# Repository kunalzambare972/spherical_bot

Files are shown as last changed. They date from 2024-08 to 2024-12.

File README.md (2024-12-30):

# Spherical-Bot

This repository encapsulates the information related to board dimensions, electronics, sensors and its testing scripts, to controller node for the development of Spherical Bot 2.0

For the software parts and test scrpits of the robot go to this repo : (https://github.com/kunalzambare972/sp-bot) 

## Table of Contents

* [Hardware](https://github.com/kunalzambare972/spherical_bot?tab=readme-ov-file#hardware)
  * [Hardware BOM](#hardware-bom)
  * [PCB Layout and BOM](#pcb-bom-and-layout)
* [Software](https://github.com/kunalzambare972/spherical_bot?tab=readme-ov-file#software)
  * [SD Card Setup](#sd-card-setup)
  * [Software Pre-Requisites](#software-pre-requisites)
  * [IMU Test](#imu-test)
  * [Picamera Test](#picamera-test)
  * [Robot Motion](#robot-motion)
* [Control](https://github.com/kunalzambare972/spherical_bot?tab=readme-ov-file#control)
  * [Pitch Control](#pitch-control)
  * [Roll Control](#roll-control)

# Hardware

## Hardware BOM

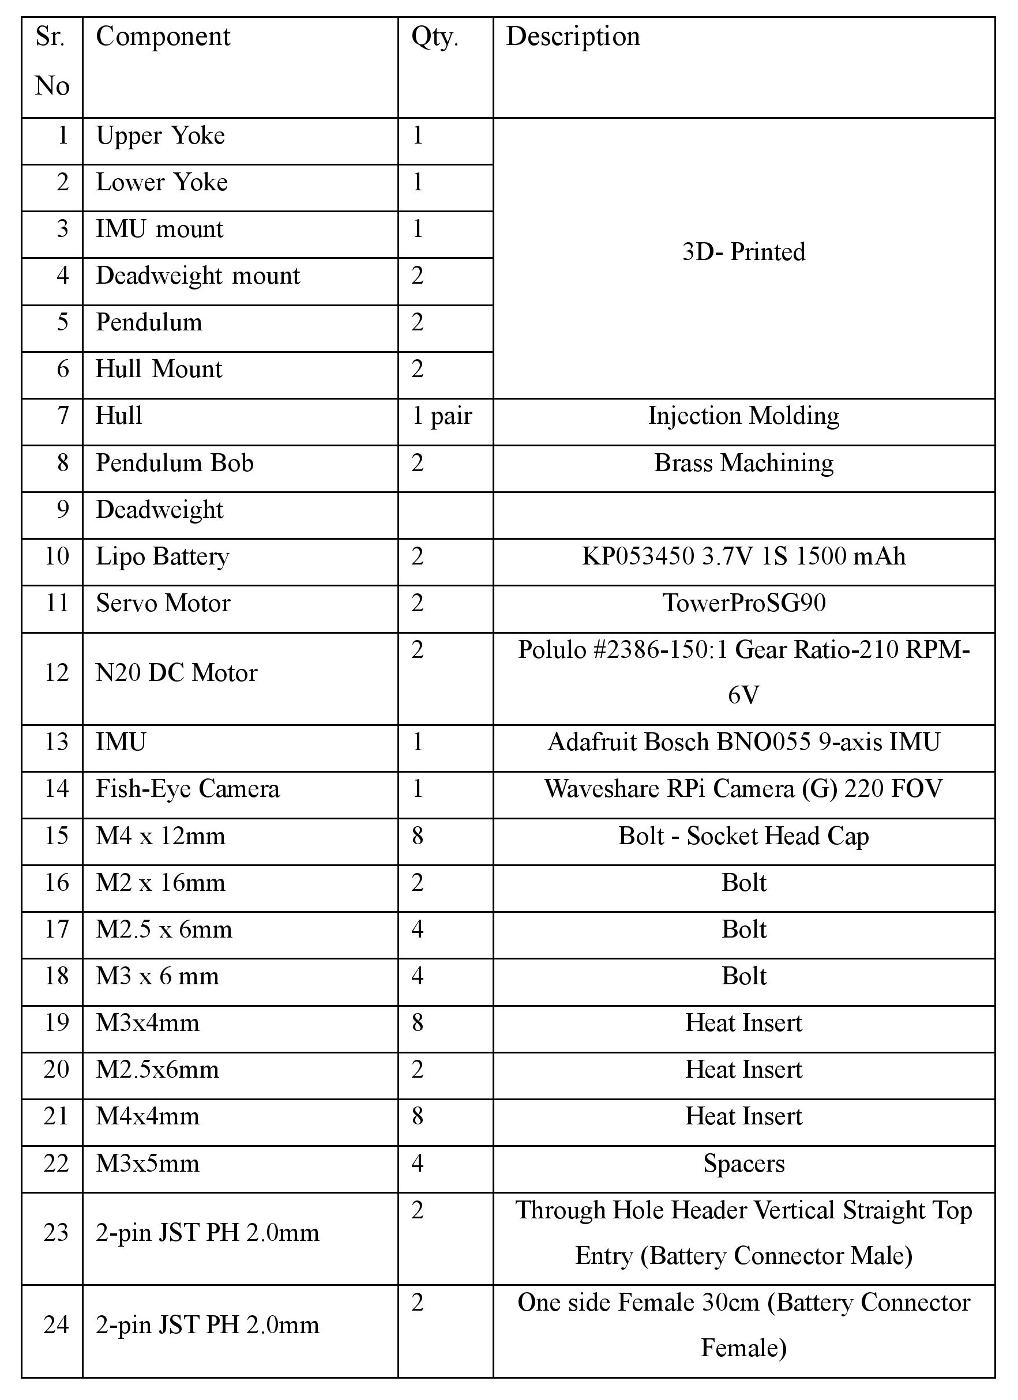
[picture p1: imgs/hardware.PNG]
<p align="center"> 
<br/>

## PCB BOM and Layout

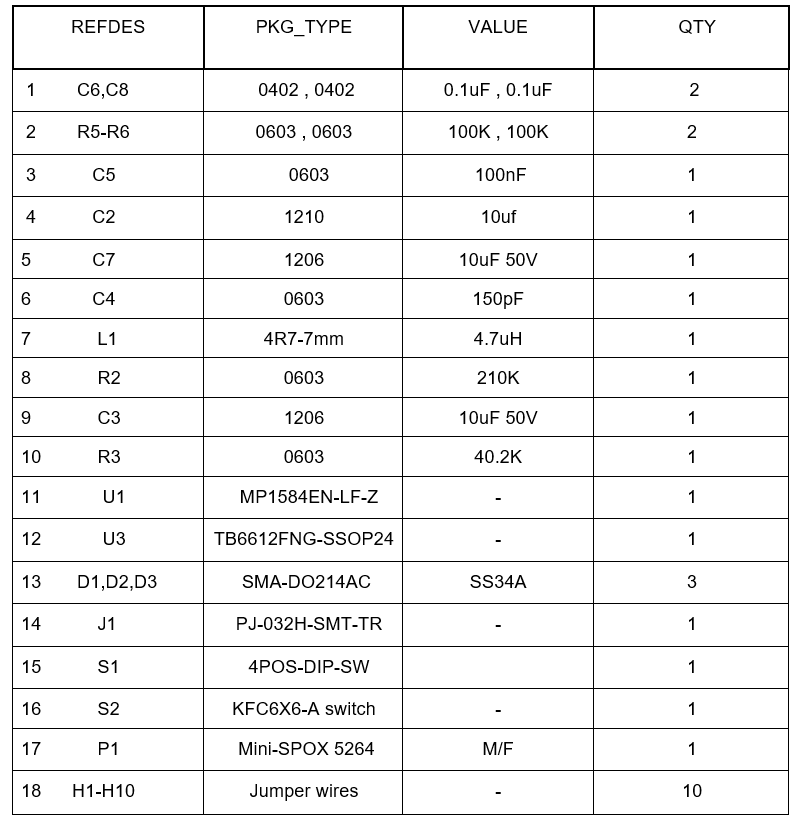
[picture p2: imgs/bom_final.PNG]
Final BOM
<p align="center"> 
<br/>

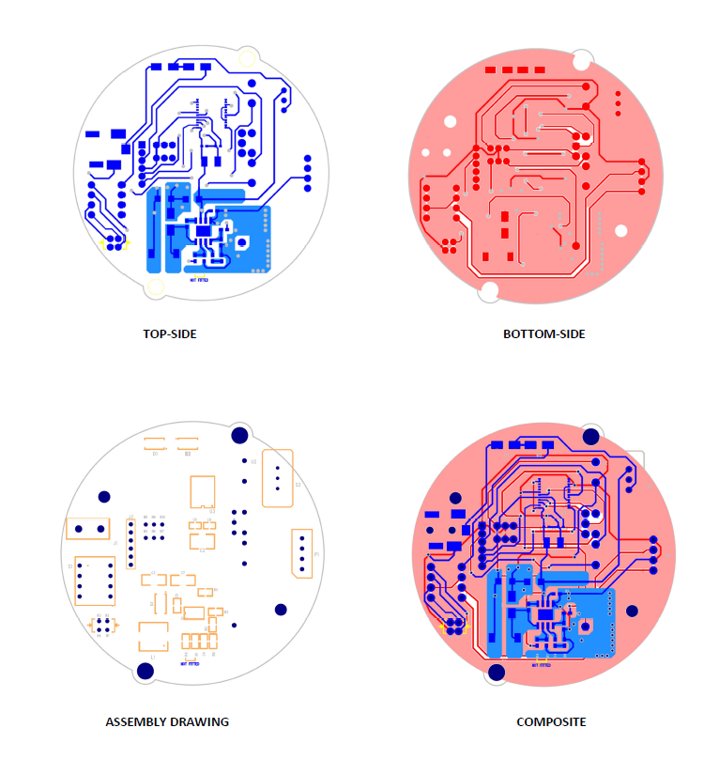
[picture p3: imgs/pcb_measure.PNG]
PCB Dim
<p align="center">
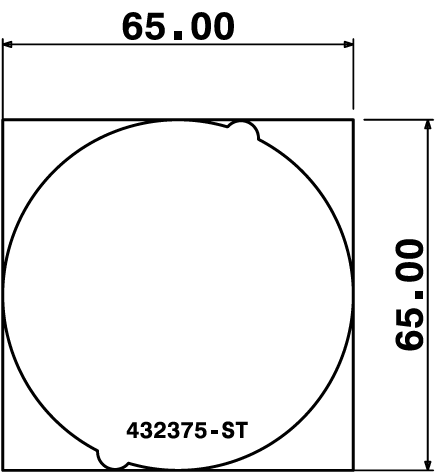
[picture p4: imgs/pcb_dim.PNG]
Overall Board Dimension


# Software

## SD Card Setup

1. Download the Raspberry Pi Imager<br/>
   The easiest way to set up an SD card is by using the Raspberry Pi Imager tool.<br/>
   i. Download Raspberry Pi Imager from the official website of raspberry pi.<br/>

2. Install Raspberry Pi Imager<br/>
   i. Windows/Mac: Run the downloaded installer and follow the on-screen instructions.<br/>
   ii. Linux: For Ubuntu, you can install it directly via the terminal:
   ```
   sudo apt install rpi-imager
   ```
3. Insert the microSD card into your computer using an SD card reader.
4. Launch Raspberry Pi Imager on your computer.
5. Choose the Device in Raspberry Pi Imager which is Raspberry Pi Zero W.
6. Choose the OS in Raspberry Pi Imager which is Raspberry Pi OS (32-bit)- Debian Bookworm.
7. Select the SD Card which is connected to the computer.
8. Advanced Settings<br/>
   i. Access the advanced settings by pressing "Ctrl+Shift+X" before clicking Next/Write.<br/>
   ii. Set the hostname to "spbot"<br/>
   iii. Set the username as "sp"<br/>
   iv. Set your password.<br/>
   v. Configure Wi-Fi: Enter your Wi-Fi SSID and password if you want the Raspberry Pi to connect to Wi-Fi automatically.<br/>
   vi. Enable the SSH in the Services Section of Advanced Settings.<br/>
   vii. Click on "SAVE"<br/>
9. Click on Next/ Write and the Raspberry Pi Imager would start to write the SD card with Raspberry Pi OS(Linux).
10. Once done eject the SD card from the computer and insert it into Raspberry Pi for first boot.
    
## Software Pre-Requisites
1. Firstly we need to clone the software package github repositroy in raspberry pi file system. Since the repository is private you need to generate a personal access token for cloning the directory<br/>
  To generate a personal access token :-<br/>
   i. Go to your Github Settings >> Developer Settings >> Personal Access Tokens.<br/>
   ii. Then click on classic token.<br/>
   iii. Select the expiration date and select "repo" in scopes for full control of private repository.<br/>
   iv. Generate and copy the token. Keep it safe; you won't be able to see it again.<br/>

2. Now open the terminal and run for cloning "sp-bot" repository
```
git clone https://github.com/kunalzambare972/sp-bot.git

```
3. Authenticate<br/>
   i.When prompted for a username, enter your GitHub username.<br/>
   ii.When prompted for a username, enter your GitHub username.<br/>
   
4. Enter the Repository Directory

```
cd sp-bot
```
   
5. Install all the required dependencies  
```
pip install -r requirements.txt
```
The above the steps would help to setup the raspberrypi sdcard for the operation of the robot

## IMU Test

The IMU being used is the Bosch 9-axis BNO-055 sensor -

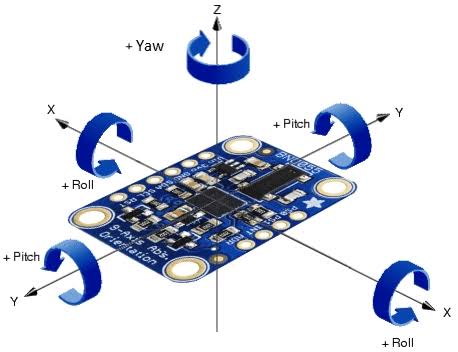
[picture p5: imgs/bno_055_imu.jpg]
BNO_IMU
<p align="center"> 
<br/>

### Plotting the IMU result

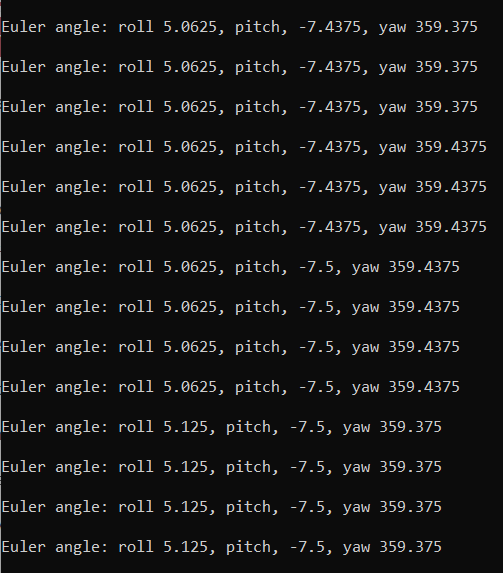
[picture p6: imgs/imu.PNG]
IMU_command_line
<p align="center">
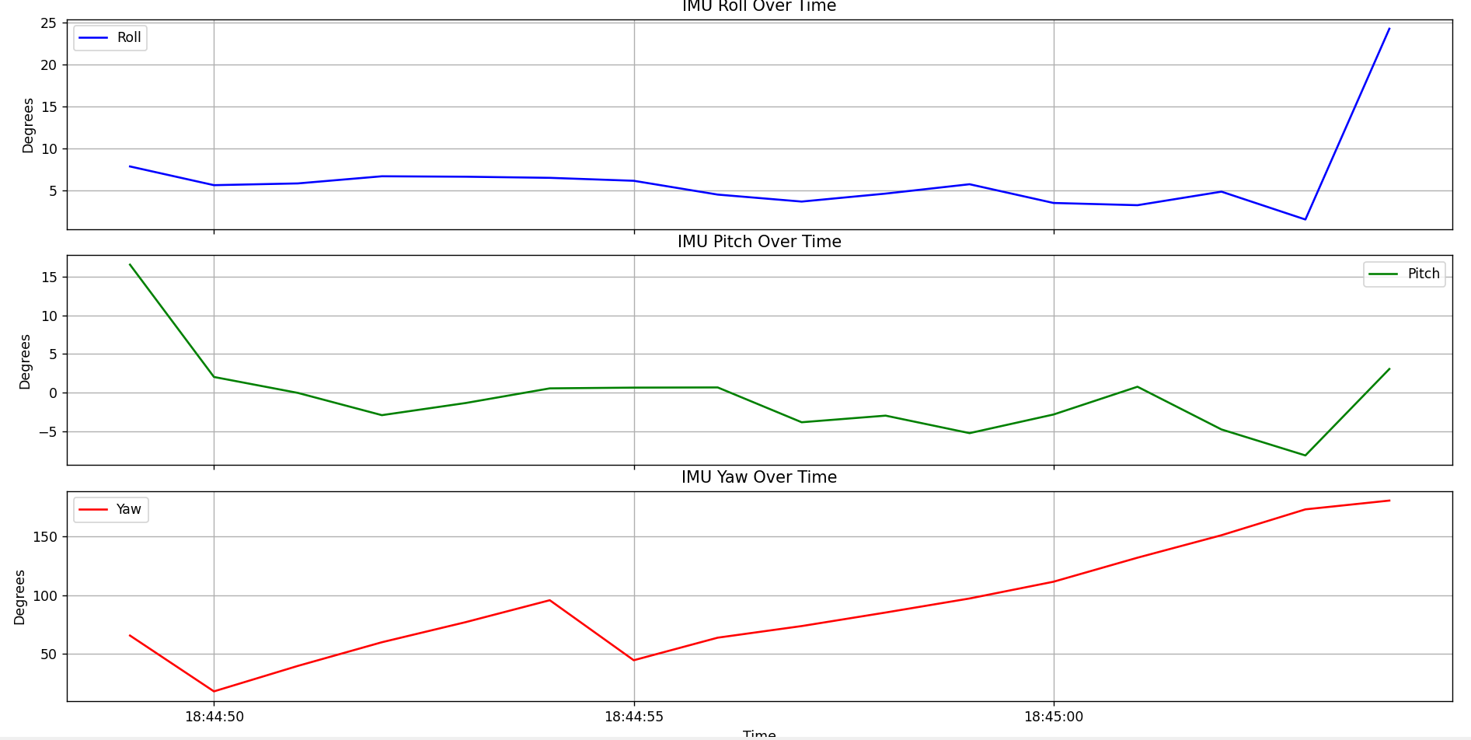
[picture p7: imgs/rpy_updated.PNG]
IMU_graph


### To test the IMU output - 

1. Navigate to sensor_tests/IMU_test directory
2. Run the test_imu.py

## PiCamera Test

The Camera being used is the Waveshare OV5647 220FOV Camera -

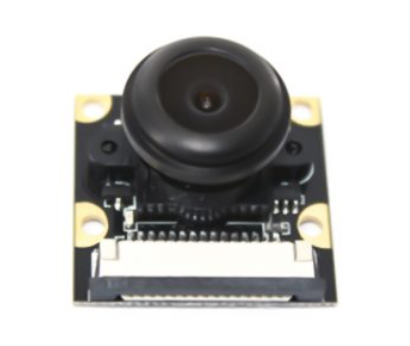
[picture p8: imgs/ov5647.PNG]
Camera
<p align="center"> 
<br/>

### Viewing the output from camera

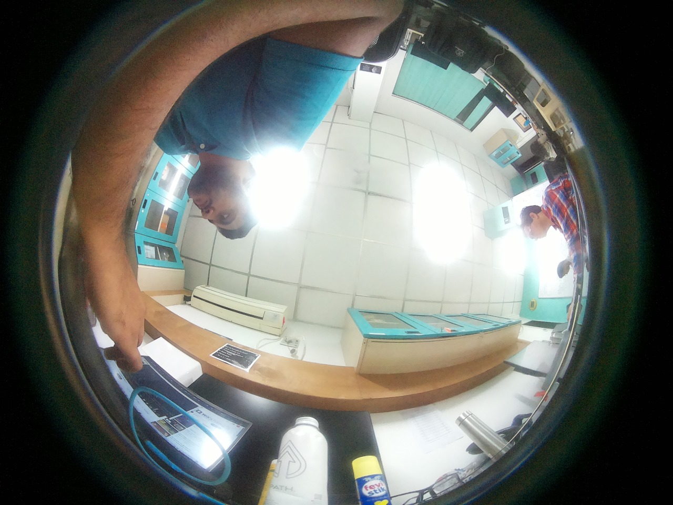
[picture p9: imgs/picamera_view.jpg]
Cam_output
<p align="center">
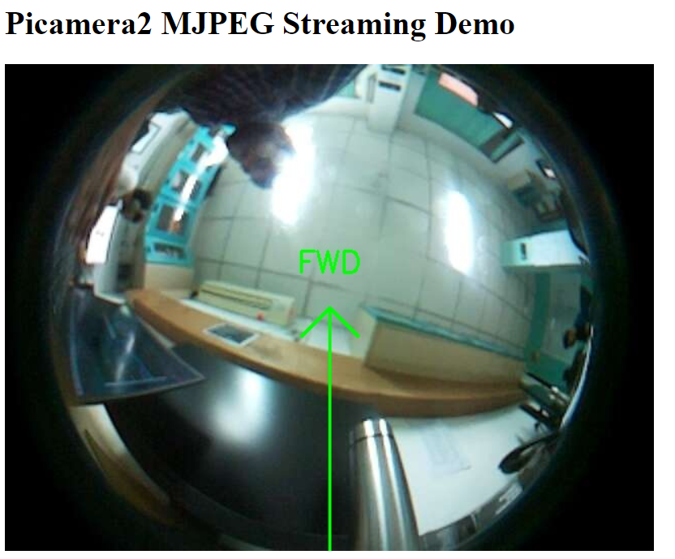
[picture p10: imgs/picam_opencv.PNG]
Cam_fw_output


### To test the camera output - 

1. Note down the system's IP
2. Navigate to sensor_tests/Picamera_test directory
3. Run the test_picam2.py
4. Head to the following page - http://{IP_ADDRESS or spbot.local}:5000/

## Robot Motion

The following clip shows the robot's forward movement - 

https://github.com/user-attachments/assets/1400048a-bb1d-4988-941b-7a97be991c32

The following clip shows the robot's forward and backward movement -

https://github.com/user-attachments/assets/daac4932-1899-4ce8-a5ff-24615ddae6e5

# Control

## Pitch Control

### Methodology
The pitch control of the Spherical Bot is managed using a Proportional Controller (P-controller). The control strategy is implemented to maintain the desired pitch angle by adjusting the servo motors and the N20 motor based on the feedback from the IMU sensor.

### Mathematical formula

The Proportional Control equation used is:

$$
P_{\text{error}} = \text{Set Point} - \text{Actual Pitch}
$$

$$
\text{Motor PWM} = \max(0, \min(200, K_p \times P_{\text{error}} + \text{User PWM}))
$$

where:
-  $$  P_{\text{error}} $$ is the pitch error.
- $$ \( \text{Set Point} \) is the desired pitch angle (set to 0.0 degrees in this case).
- $$ \( \text{Actual Pitch} \) is the current pitch angle measured by the IMU sensor.
- $$ \( K_p \) is the proportional gain, set to 0.00876.
- $$ \( \text{User PWM} \) is a constant value (set to 185) that provides the base motor speed.
- $$ \( \text{Motor PWM} \) is the calculated PWM value to drive the motor, ensuring it stays within the range of 0 to 200

### Optimal Value

The optimal proportional gain $$ (\( K_p \)) for achieving stable pitch control is determined to be:

$$ \[ K_p = 0.00876 \]

## Roll Control

### Methodology

The roll control of the Spherical Bot is managed using a Proportional Controller (P-controller). The control strategy is implemented to maintain the desired roll angle by adjusting the servo motors and the N20 motor based on feedback from the IMU sensor.

### Mathematical Formula

The Proportional Control equation used is:

$$
P_{\text{error}} = \text{Set Point} - \text{Actual Roll}
$$

$$
\text{Motor PWM} = \max(0, \min(200, K_p \times R_{\text{error}} + \text{User PWM}))
$$

where:
- \( R_{\text{error}} \) is the roll error.
- \( \text{Set Point} \) is the desired roll angle (set to 0.0 degrees in this case).
- \( \text{Actual Roll} \) is the current roll angle measured by the IMU sensor.
- \( K_p \) is the proportional gain, set to 0.00876.
- \( \text{User PWM} \) is a constant value (set to 185) that provides the base motor speed.
- \( \text{Motor PWM} \) is the calculated PWM value to drive the motor, ensuring it stays within the range of 0 to 200.

### Optimal Value

The optimal proportional gain (\( K_p \)) for achieving stable roll control is determined to be:

\[ K_p = 0.00876 \]

## License

This project is licensed under the MIT License - see the [LICENSE](LICENSE) file for details.

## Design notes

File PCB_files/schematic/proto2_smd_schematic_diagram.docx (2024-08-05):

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
10uF 5~~0V~~

100K

C5

U1 ⁸

BST

⁷VIN

100nF 1

L1

4.7 uH

15uH

22uF 6~~.3V~~

OUT

GND

C1

42 31

R4

2

SW

4

D3

10

C3

8642

GND GND

GND

6

EN

FREQ

FB

CMP

GND

3

C4

GND GND R2

210K

B

H3 H4 H2 H1 +ve2

7531

S1

GND

R1

24.9K 100K R5

5

GND

150pF

40.2K

R3

B

+ve1

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
³ IO1

GND GND

100K

R6

GND

GND

3

V

3

27

~~C~~1

28

~~C~~2

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
IO10 IO11 IO12 IO13 IO14 IO15 IO16 IO17 IO18 IO19 IO20 IO21 IO22 IO23 IO24 IO25 IO26

5

7

8

10 11 12 13 15 16 18 19 21 22 23 24 26 29 31 32 33 35 36 37 38 40

Pin 13 -> Pin 19 STBY Motor driver OUT

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
G1G2G3G4G5G6G7G8

4

0

5

0

4

9

A

691GND

2

2

3

3

U3

3

C8

0.1uF GND

A

C1 C2

¹ A01

VM1

24

VIN

OUT GND

4 1

3 2 J2

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
A01_1

PGND1

PGND1_1 A02

A02_1

B02

B02_1

PGND2

PWMA AIN2 AIN1 VCC

STBY GND

BIN1 BIN2

23 22 21 20 19 18 17 16

C2

10uF

C6

0.1uF

TITLE

Schematic1

Corrected Schematic

10

11

GND

12

GND

PGND2_1 B01

B01_1

PWMB VM3 VM2

15 14 13

GND

1

DWG NO001 modified by Akash Shenil

MODIFIED BY

AKASH SHENIL

SIZE REV A4

DRAWN BY

GIRISH GIRI

SCALE of

SHEET

INCH 1 2 24/02/2020:21:56 27/09/2023 27/09/2023

27-09-2023

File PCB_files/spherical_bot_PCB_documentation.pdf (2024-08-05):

# SPHERICAL BOT

## DUAL-LAYER, UTILITY CIRCUIT BOARD

### DESCRIPTION

The Utility Circuit Board (UCB) is adual-layer, surface mount technology-based board designed to combine 3+ functional blocks on a single PCB. The objective is to achieve modularity, minimize repair and diagnostic issues with a form factor optimum to the SPEHRICAL BOT mechanical constraints.

### FEATURES

The UCB features following utilities:

- MP1584 - 3A, 1.5MHz, 28V Step Down Converter Logic.
- TB6612FNG – 4 mode Motor Driver Logic.
- Raspberry Pi Zero W compatibility.
- Charging Mode with Dual Series Battery input and External Supply Logic.
- Reverse current protection logic.

### APPLICATIONS

- Power Input.
- Battery Charging.
- Control In/Outs.
- High voltage conversion.
- Current Conversion.
- Reverse Input Protection.

### SOFTWARE

The schematic for PCB is designed on DxDesigner Software. The layout is designed and developedon PADS v9.5 and both these platforms are a part of software package tool suite from Mentor Graphics, Siemens. The schematic design is developed by implementing universal standard symbol library and can be used to migrate decal layout libraries in PADS logic for layout designing. The foot print for each component is developed from scratch by referring to respective datasheet constraints for decal guidelines.
The routing for layout is developed with optimum designing rules for trace length and width. The board design ensures all requisite IPC standard and EMI, EMC considerations are met. All placements and routing are done with strictly referring to PCB layout Guidelines wherever needed and mentioned in components datasheets.

### BLOCK DIAGRAM

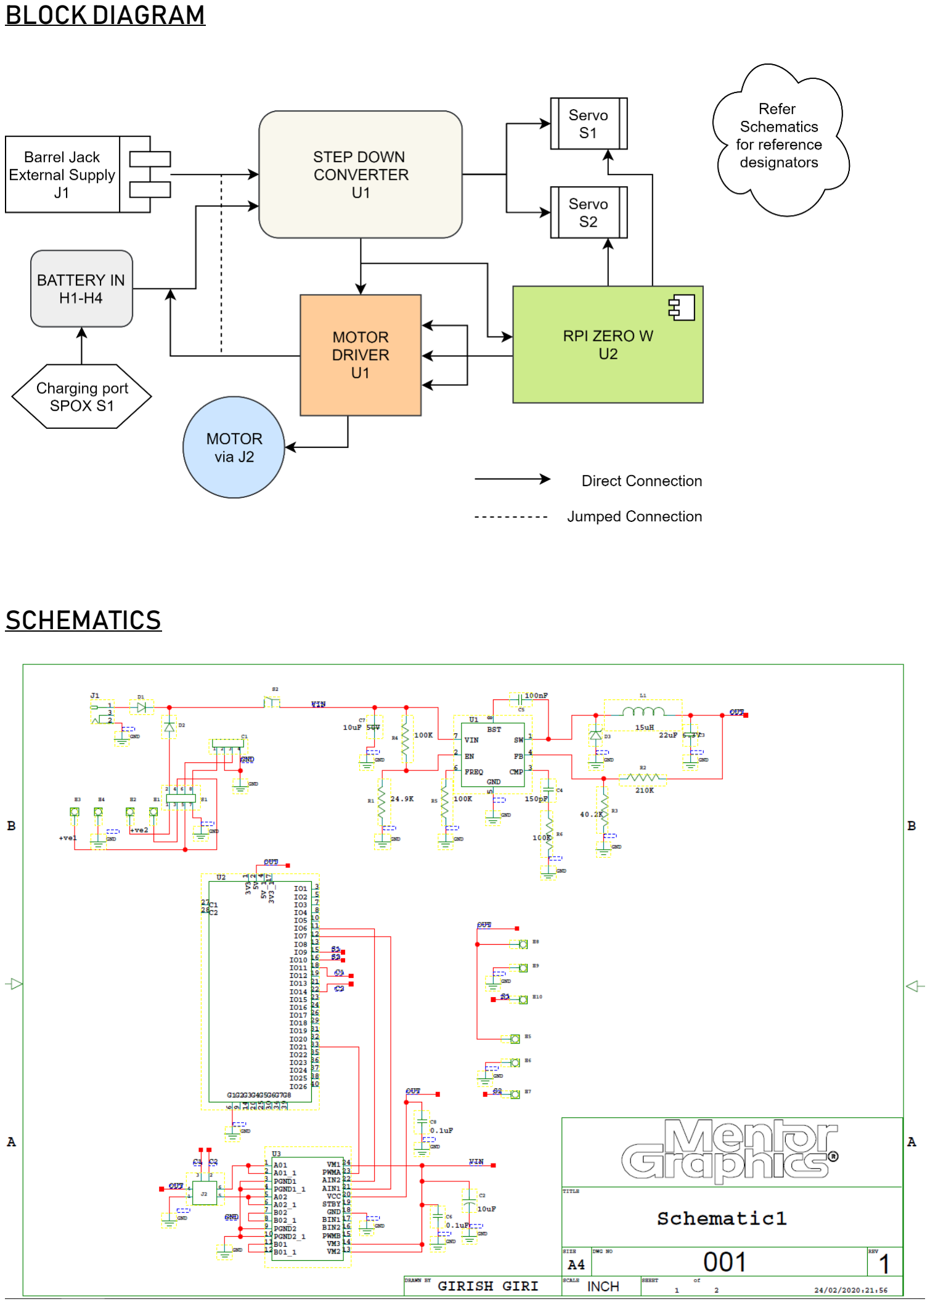
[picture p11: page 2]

### SCHEMATICS

### LAYOUT

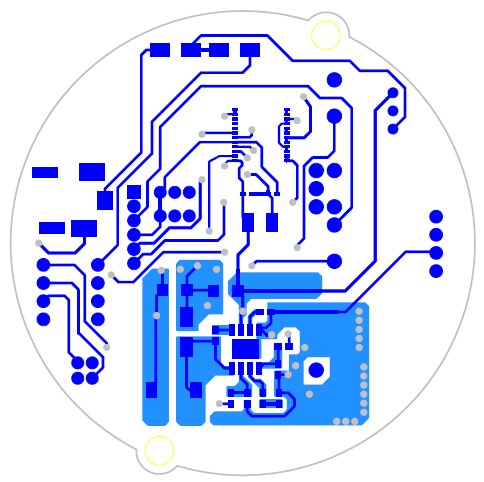
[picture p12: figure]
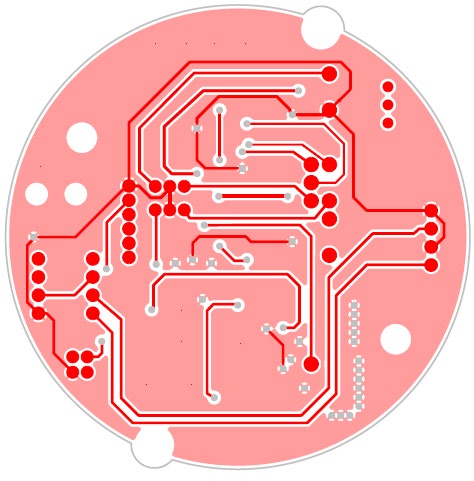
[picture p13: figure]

TOP-SIDE | BOTTOM-SIDE

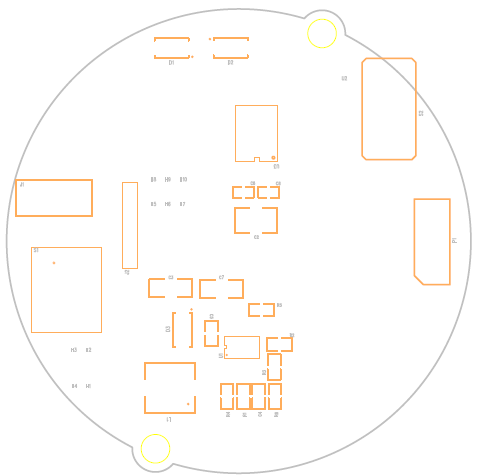
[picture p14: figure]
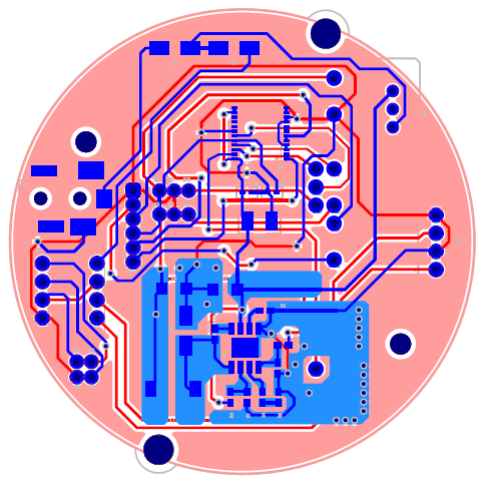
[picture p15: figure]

ASSEMBLY DRAWING | COMPOSITE

### CAD MODELLING

The PADS layout file designed for the PCB is exported in CAM planes to generate GERBER files for PCB Fabrication. The same Layout File can be exported in .iso format supported in CircuitWorks, which is an extension available in SolidWorks 2017. CircuitWorks allows user to view the layout design into actual 3D phase and also features editable components library which can be updated by manually searching for the part files of each component online and adding it in the same. Once all components are added, the build command generates and assembly file with available components mounted on board as shown in figure above. The above process gives a very near perfect idea about the utility board before its fabrication and assembly.

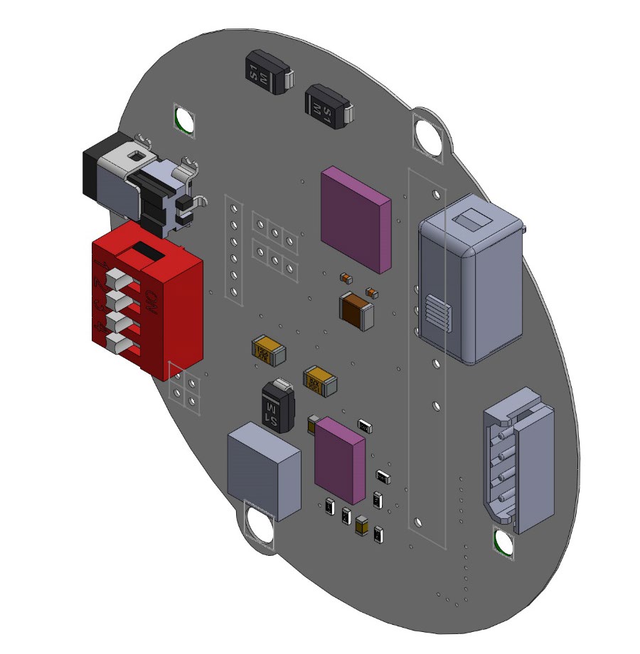
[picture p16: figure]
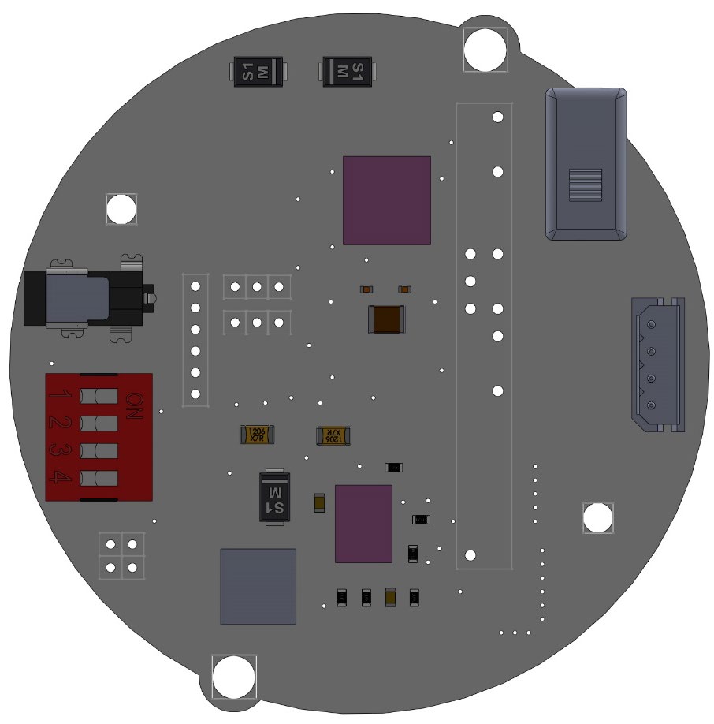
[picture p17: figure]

Almost all the components (SMD and Through Hole) are mounted on top side to maintain isolation with motors at the bottom. The utility board is designed to sustain permissible current and voltage
ratings | provided | by
manufacturers, | with
consideration of safe positive
tolerance | values. | The
components selection is based on ratings and package availability. The placement of each device is done to ensure compatibility with bot mechanics keeping accessible terminals exposed. Thermal areas and isolations are provided wherever required for heat dissipation.

### REFERENCES

Kindly refer to Datasheets, BOM, Schematics and Layout Docs and CAD drawings from the PCB Fabrication and Development Folder Zip folder for design logic, component values/counts, package types, Drill Holes, Board Outline, specifically Components datasheet for PCB Layout Guidelines, Fabricator details and other relevant information.

### NOTE

The information in this document is subject to changes but should only be done with prior notice to Vaibhav Kadam, Research Assistant Spherical Bot. The information changes should be only in the form of an update, any direct changes require notification from the user. Users should warrant and guarantee that no information and data is manhandled, misplaced or affected in a way that leads to additional work of already done job. The data in this Document and all the other relevant information in PCB Fabrication and Development Folder Zip is abides by the said disclaimer.

# SPHERICAL BOT

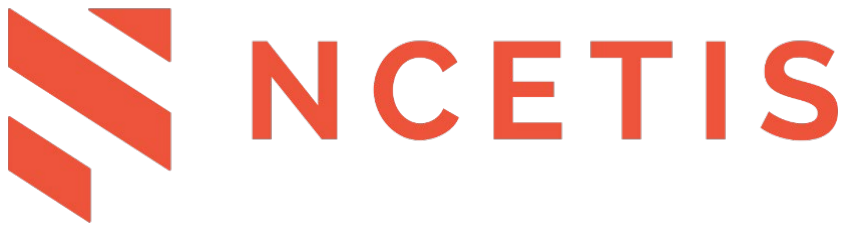
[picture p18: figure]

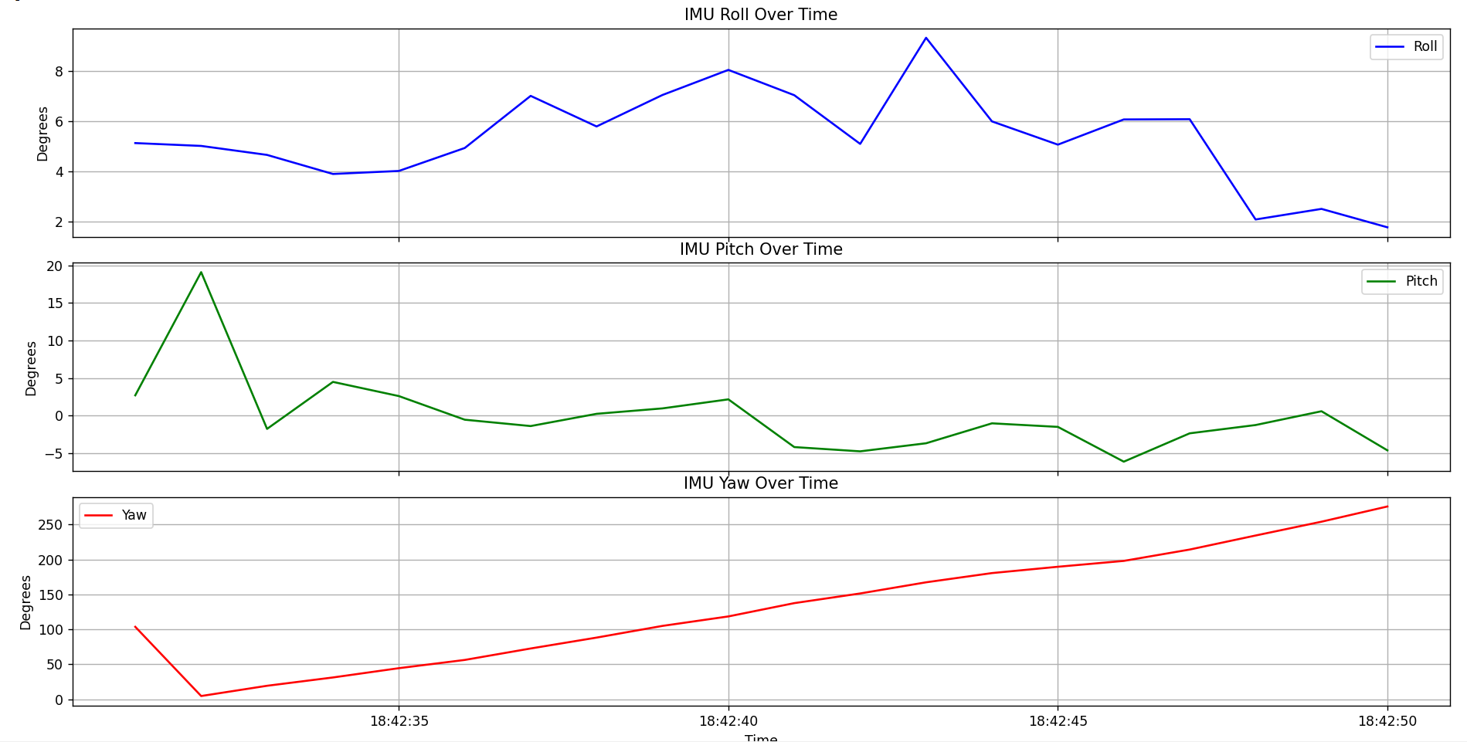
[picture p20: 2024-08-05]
imgs/rpy_updated_2.PNG

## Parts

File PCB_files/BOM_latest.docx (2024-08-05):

Part Lister output for Board1

Generated on Monday, February 24, 2020

Modified on Thursday, October 5, 2023 by Akash Shenil.

REFDES | PKG_TYPE | VALUE | QTY
1 C6,C8 | 0402 , 0402 | 0.1uF , 0.1uF | 2
2 R5-R6 | 0603 , 0603 | 100K , 100K | 2
3 C5 | 0603 | 100nF | 1
4 C2 | 1210 | 10uf | 1
5 C7 | 1206 | 10uF 50V | 1
6 C4 | 0603 | 150pF | 1
7 L1 | 4R7-7mm | 4.7uH | 1
8 R2 | 0603 | 210K | 1
9 C3 | 1206 | 10uF 50V | 1
10 R3 | 0603 | 40.2K | 1
11 U1 | MP1584EN-LF-Z | - | 1
12 U3 | TB6612FNG-SSOP24 | - | 1
13 D1,D2,D3 | SMA-DO214AC | SS34A | 3
14 J1 | PJ-032H-SMT-TR | - | 1
15 S1 | 4POS-DIP-SW | | 1
16 S2 | KFC6X6-A switch | - | 1
17 P1 | Mini-SPOX 5264 | M/F | 1
18 H1-H10 | Jumper wires | - | 10

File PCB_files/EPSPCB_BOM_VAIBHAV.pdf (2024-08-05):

Part Lister output for Board1
Generated on Monday, February 24, 2020
# | REFDES | PKG_TYPE | VALUE | QTY

| 1 C6,C8 | 0402,0402 | 0.1uF,0.1uF | 2
| 2 R4-R6 | 0603,0603,0603 | 100K,100K,100K | 3
| 3 C5 | 0603 | 100nF | 1
| 4 C2 | 1210 | 10uF | 1
| 5 C7 | 1206 | 10uF 50V | 1
| 6 C4 | 0603 | 150pF | 1
| 7 L1 | 4R7-7MM | 15uH | 1
| 8 R2 | 0603 | 210K | 1
| 9 C3 | 1206 | 22uF 6.3V | 1
10 R1 | 0603 | 24.9K | 1
11 R3 | 0603 | 40.2K | 1
12 U1 | MP1584EN-LF-Z | - | 1
13 U3 | TB6612FNG-SSOP24 | - | 1
14 D1-D2 | SMA-DO214AC | 40V 3A | 2
15 D3 | SMA-DO214AC | SS34 | 1
16 J1 | PJ-032H-SMT-TR | - | 1
17 S1 | 4POS-DIP-SW | - | 1
18 S2 | 25136N B | - | 1
19 P1 | Mini-SPOX 5264 | M/F | 1
20 H1-H60 | Header-Male-2.54 | - | 2x40

I have labelled all the ref des for the given component.

#7 L1 desolder 4R7 inductor from given breakout board.

#20 H1-H60 do not solder leave it as it is

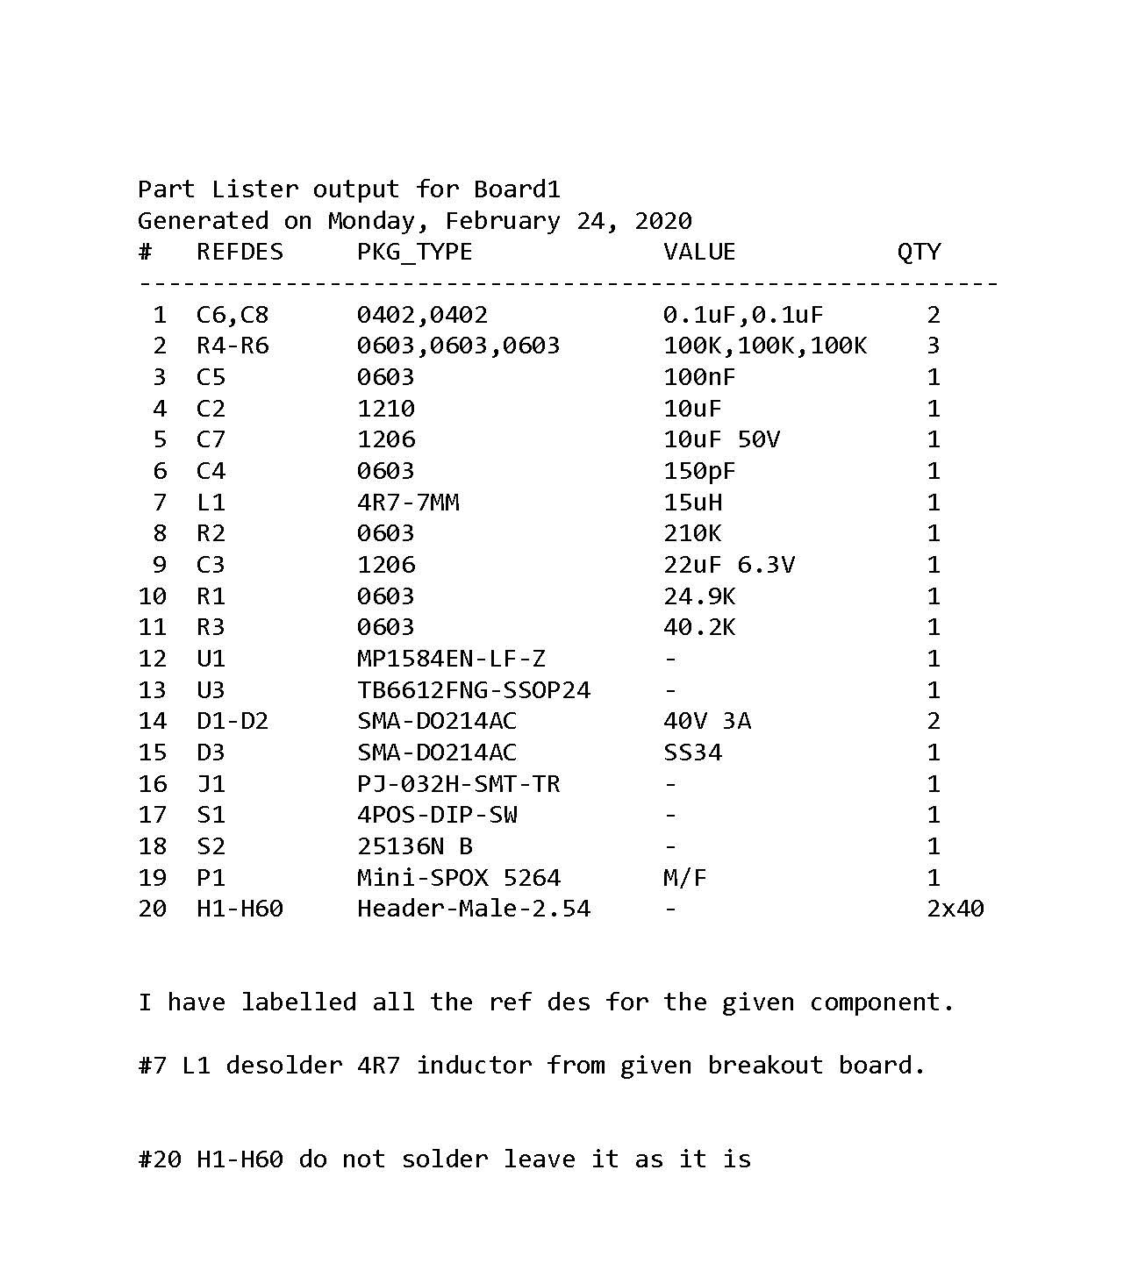
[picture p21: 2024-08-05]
PCB_files/EPSPCB_BOM_VAIBHAV.jpg

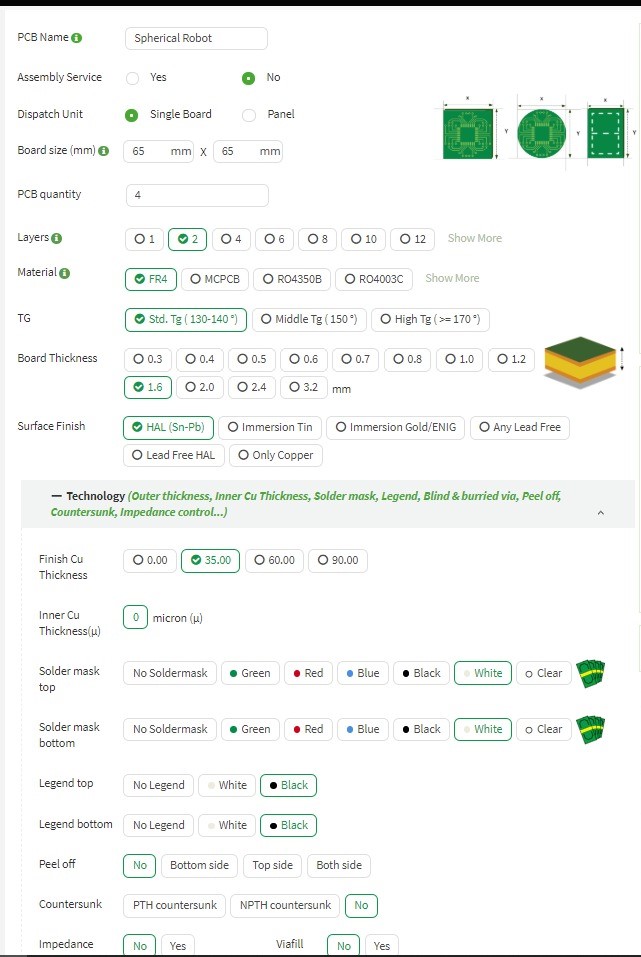
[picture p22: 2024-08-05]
PCB_files/PCB_requirements&power/How to Order/Order preference.jpeg

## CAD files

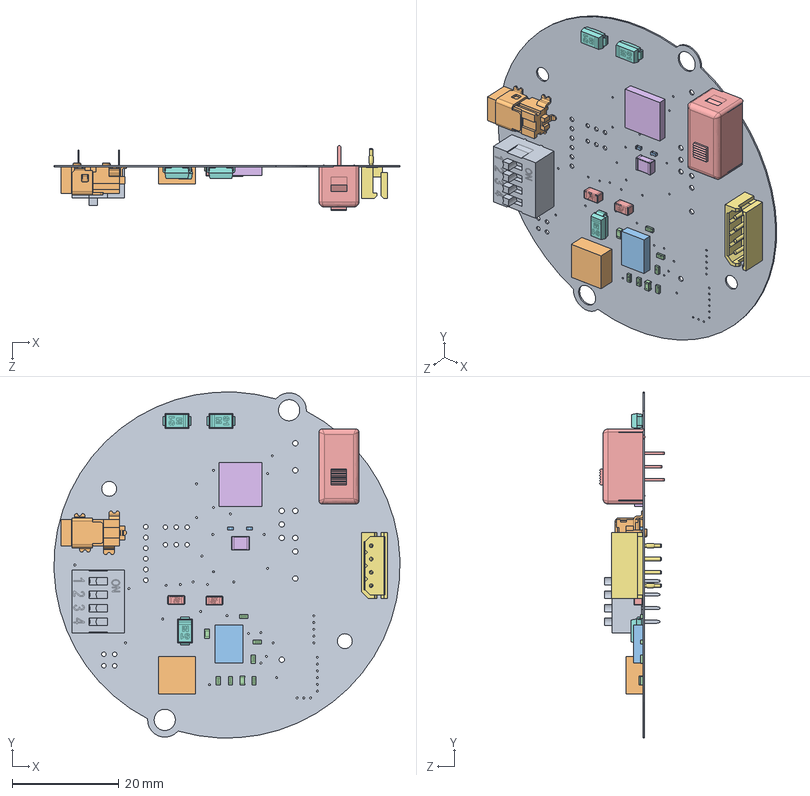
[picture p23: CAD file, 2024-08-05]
PCB_files/CAD_assembly/FINAL PCB CAD/sb.SLDASM
65.0 x 64.9 x 12.2 mm
sb
pj-032h-smt-tr
0402c_2320560 x 2
0603C x 2
Capacitor Vishay 1206 X7R x 2
CAP1210
PORT
DO-214AC x 3
DS-4
inductor7mm
SOIC8_MP1584_BUCK_MP1584_BUCK
0603_RES x 6
25136nab
SSOP24_TB6612FNG_MTR_DRVR_TB6612FNG_MD

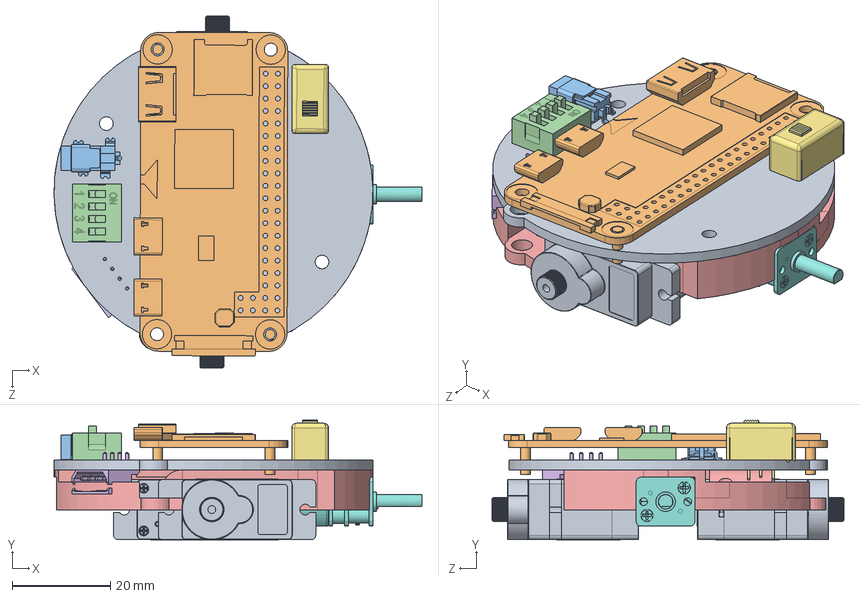
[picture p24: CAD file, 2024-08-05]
PCB_files/CAD_assembly/PCB_Placement.SLDASM
75.0 x 24.5 x 71.7 mm
PCB_Placement
Pi_Zero_W
Barrel_jack
DS-4
25136nab
N20_motor_magnetic_encoder
Servo_motor x 2

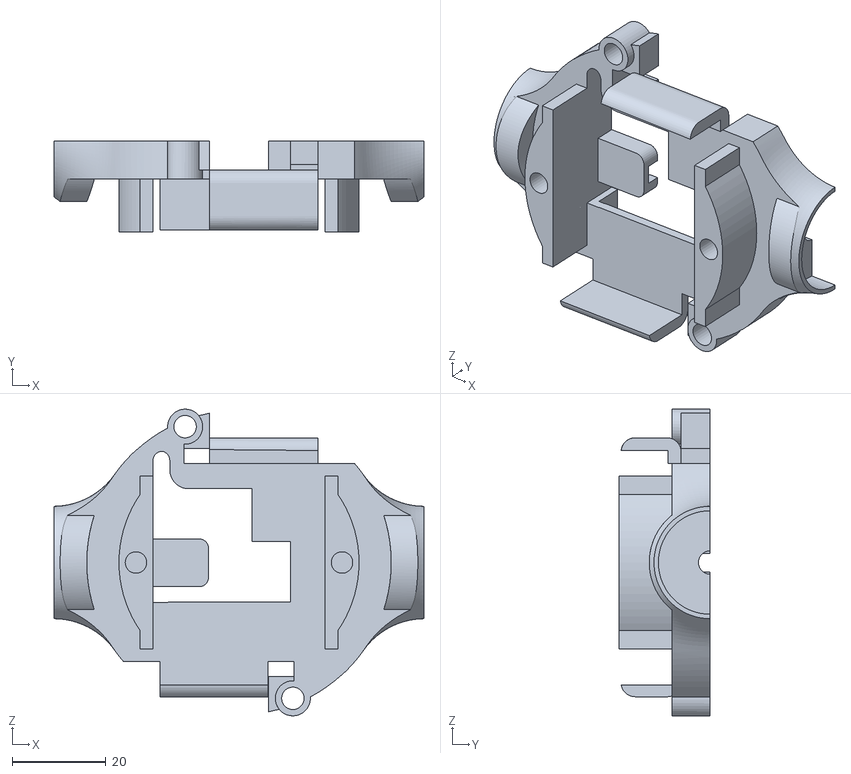
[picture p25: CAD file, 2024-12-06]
design/stl/lower_yoke.stl
79.0 x 19.5 x 65.5

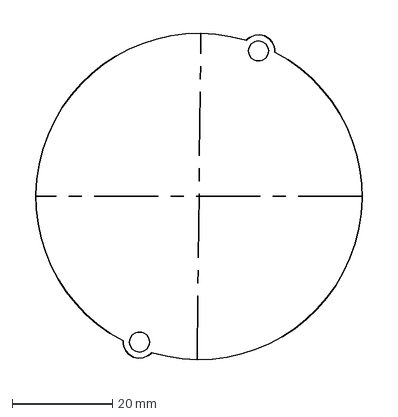
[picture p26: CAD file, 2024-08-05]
PCB_files/CAD_assembly/Part1.DXF
72.8 x 71.9 mm

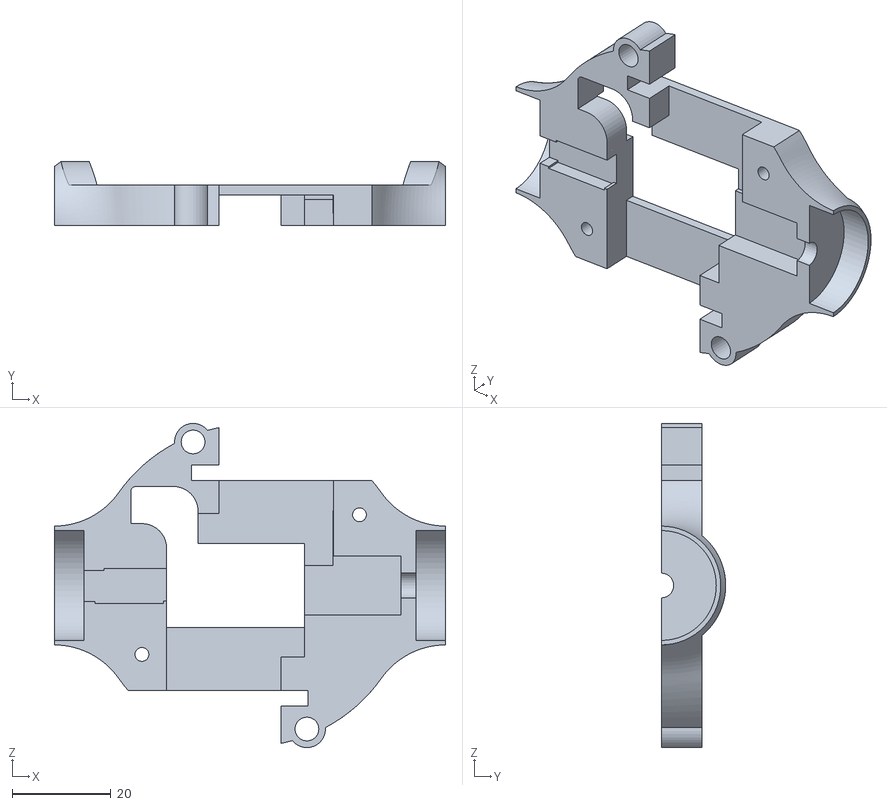
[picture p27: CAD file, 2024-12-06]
design/stl/upper_yoke.stl
79.0 x 13.0 x 65.5

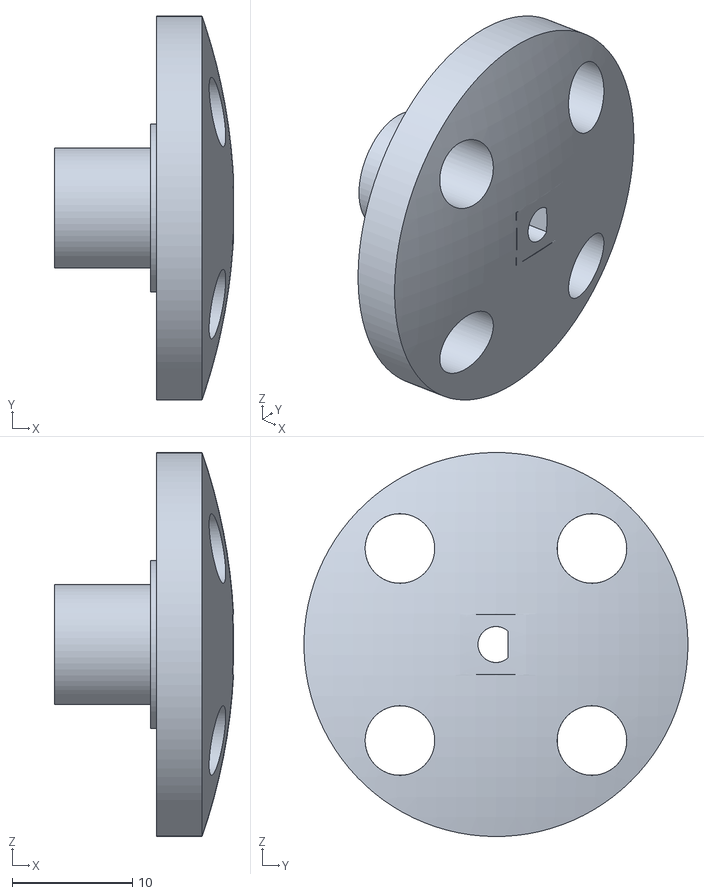
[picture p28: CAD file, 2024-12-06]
design/stl/motor_coupling.stl
14.9 x 32.0 x 32.0

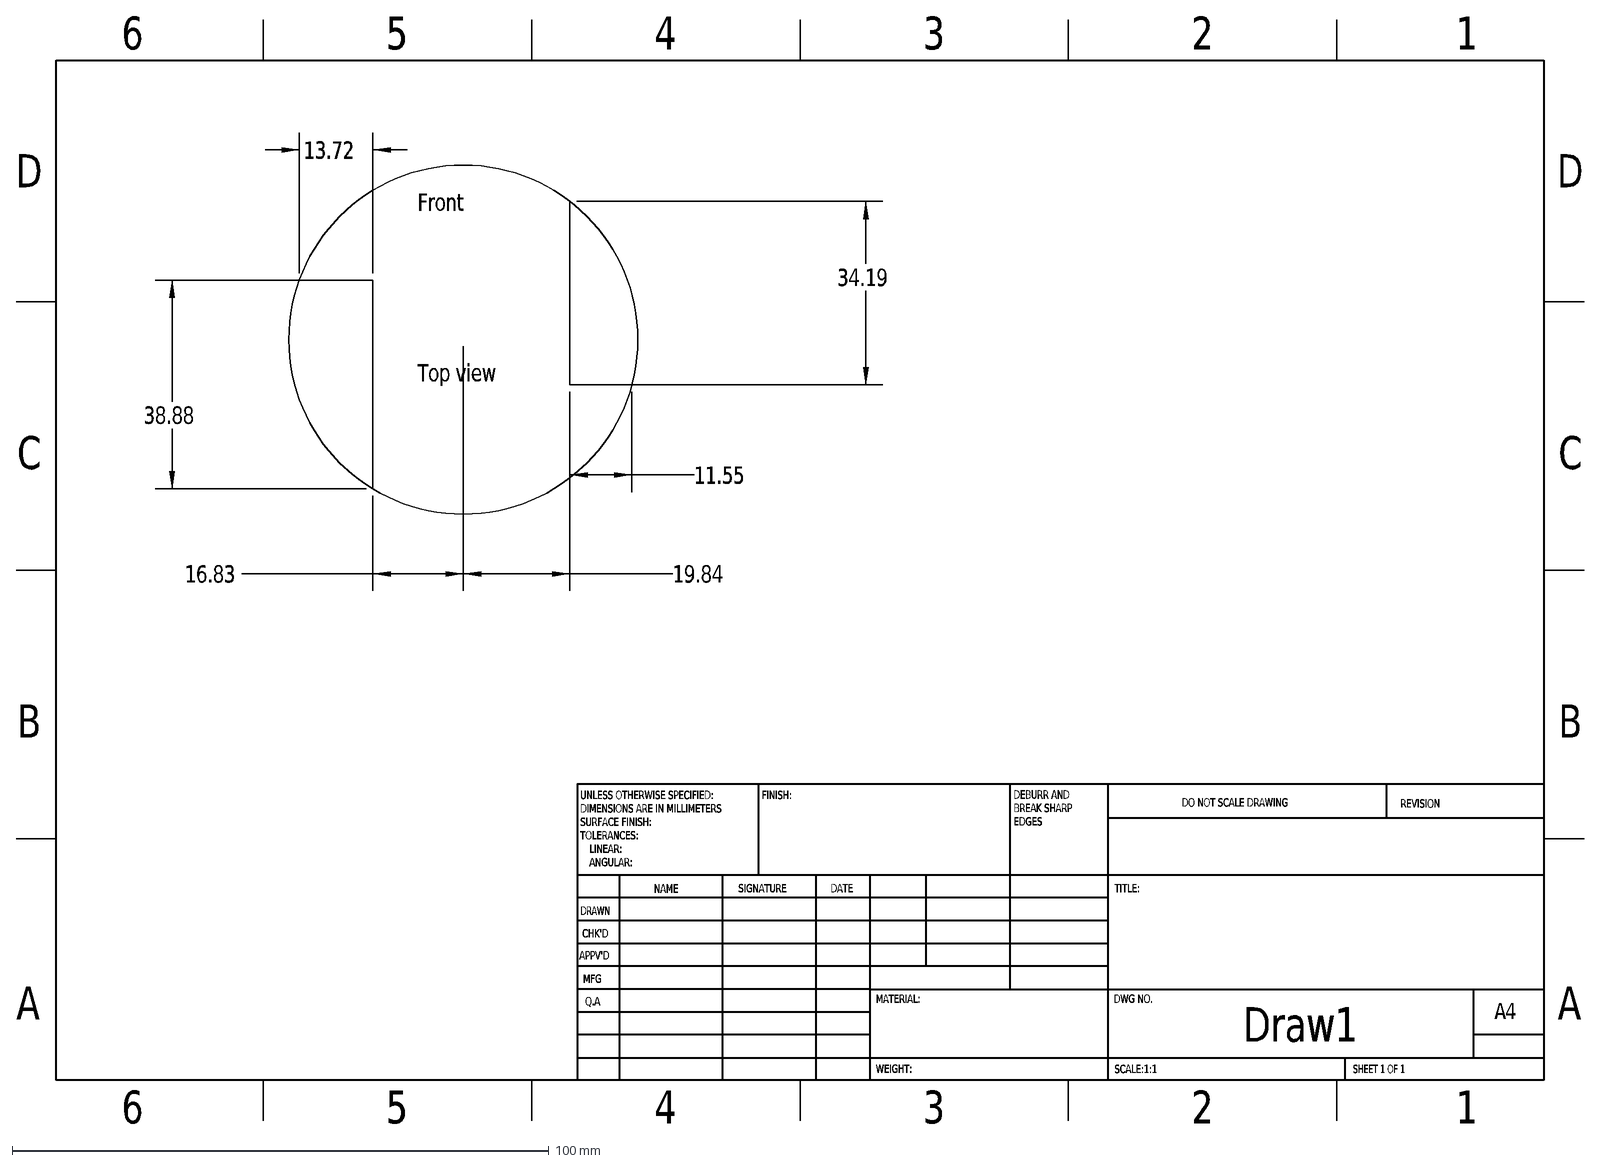
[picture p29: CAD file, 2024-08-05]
PCB_files/CAD_assembly/PCB_Layout_plan.DXF
38.88
11.55
34.19
13.72
19.84
16.83
Top view
Front
A
B
C
D
6
5
4
3
2
1
DRAWN
CHK'D
APPV'D
MFG
Q.A
UNLESS OTHERWISE SPECIFIED:
DIMENSIONS ARE IN MILLIMETERS
SURFACE FINISH:
TOLERANCES:
LINEAR:
ANGULAR:
FINISH:
DEBURR AND
BREAK SHARP
EDGES
NAME
SIGNATURE
DATE
MATERIAL:
DO NOT SCALE DRAWING
REVISION
TITLE:
DWG NO.
SCALE:1:1
SHEET 1 OF 1
A4
WEIGHT:
Draw1

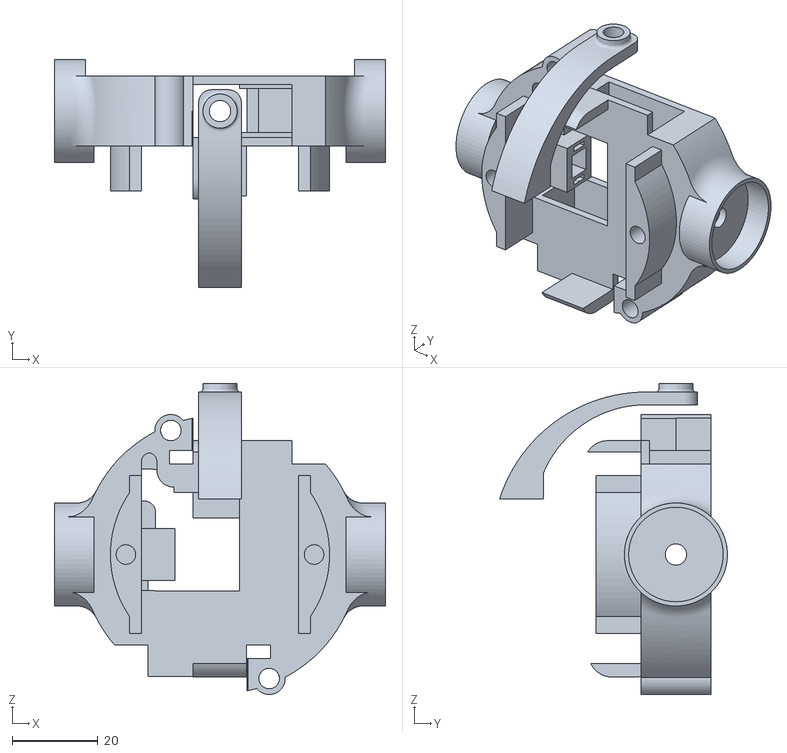
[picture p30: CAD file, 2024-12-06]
design/stl/pendulam.stl
77.4 x 53.3 x 72.7

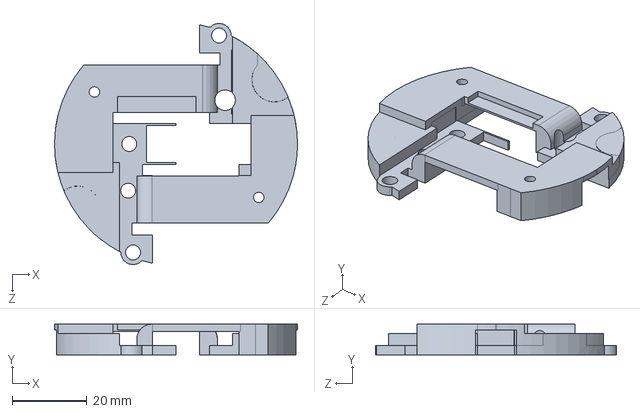
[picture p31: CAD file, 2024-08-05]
PCB_files/CAD_assembly/Yoke_Upper_PCB.SLDPRT
65.0 x 8.20 x 64.5 mm

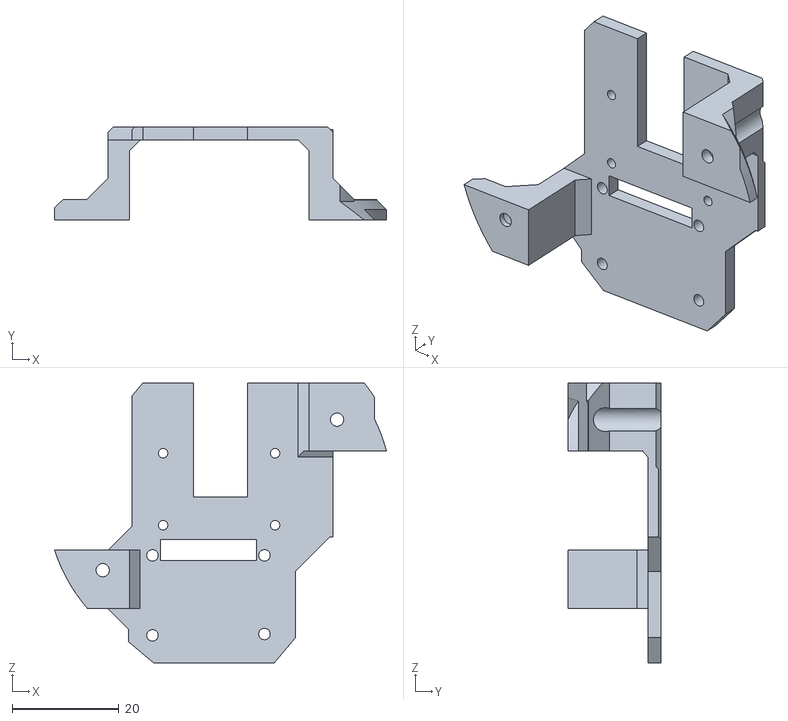
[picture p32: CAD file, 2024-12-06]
design/stl/imu_camera_mount.stl
62.3 x 17.5 x 52.5

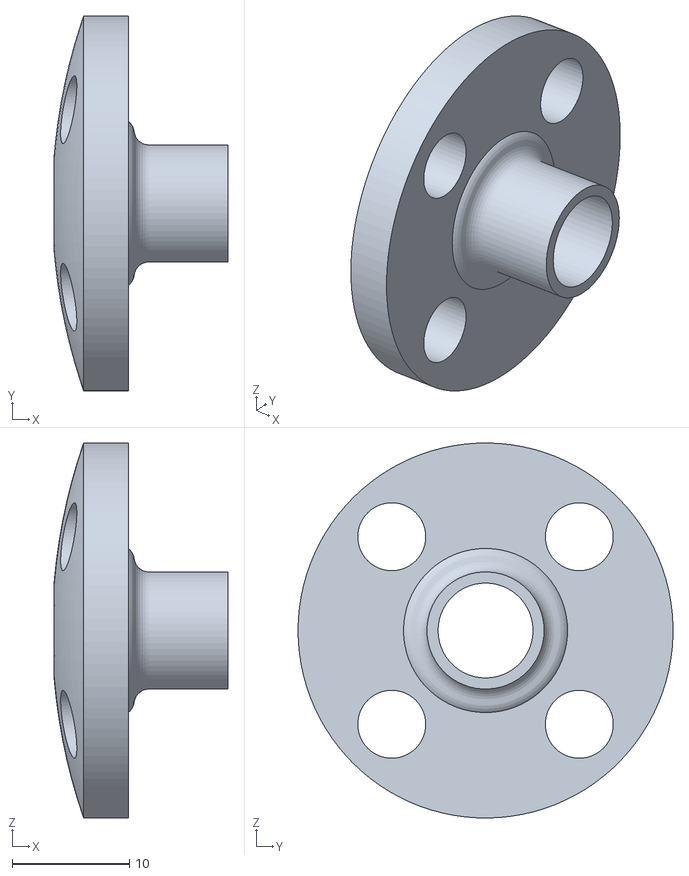
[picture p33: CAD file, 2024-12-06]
design/stl/charing_coupling.stl
14.8 x 32.0 x 32.0

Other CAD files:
PCB_files/CAD_assembly/FINAL PCB CAD/sphericalbot.SLDPRT
PCB_files/CAD_assembly/PCB_Layout_plan.SLDDRW
PCB_files/CAD_assembly/PCB_Placement.SLDPRT
design/cad_files(.f3d)/charing_coupling.f3d
design/cad_files(.f3d)/imu_camera_mount.f3d
design/cad_files(.f3d)/motor_coupling.f3d
design/cad_files(.f3d)/pendulam.f3d

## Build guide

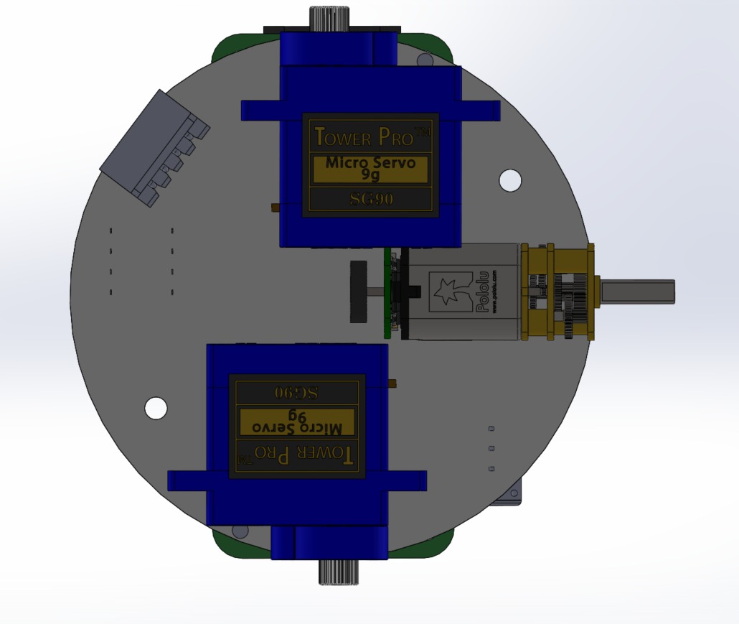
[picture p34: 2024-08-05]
PCB_files/CAD_assembly/WhatsApp Image 2020-02-27 at 4.59.00 PM.jpeg

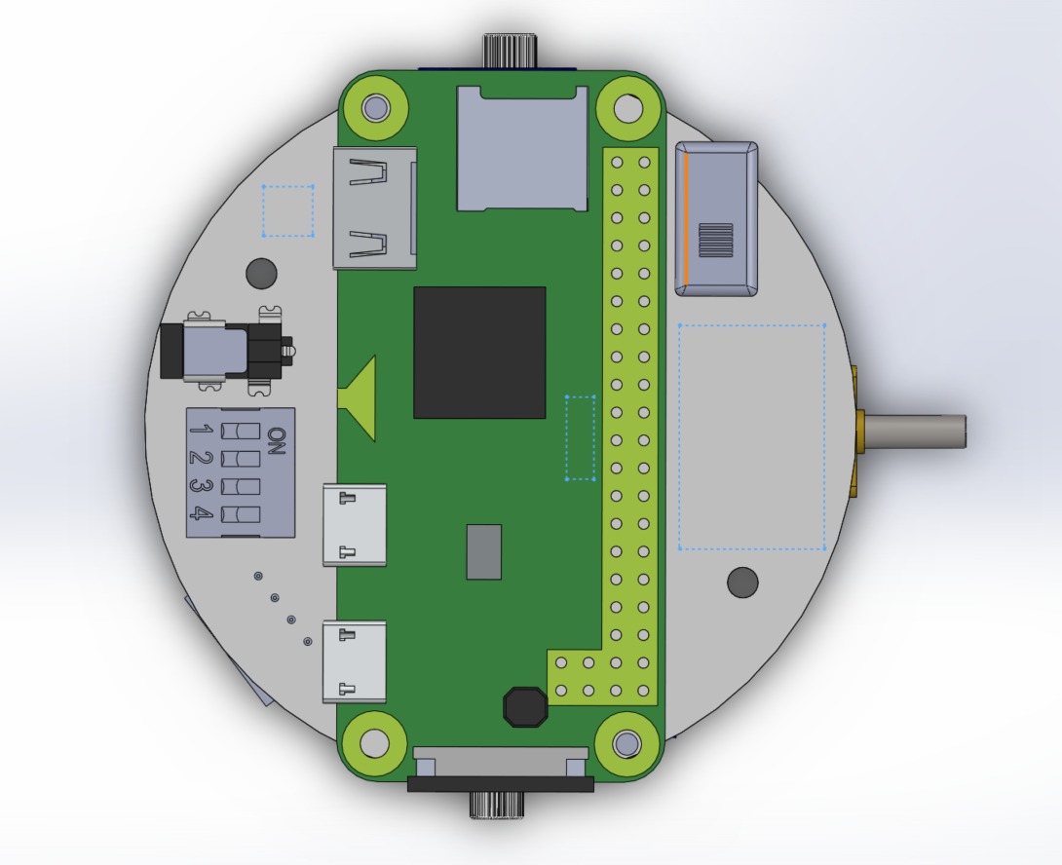
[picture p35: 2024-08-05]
PCB_files/CAD_assembly/WhatsApp Image 2020-02-27 at 4.58.12 PM.jpeg

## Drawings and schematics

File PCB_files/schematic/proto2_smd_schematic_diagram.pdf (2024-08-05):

U1 8 5

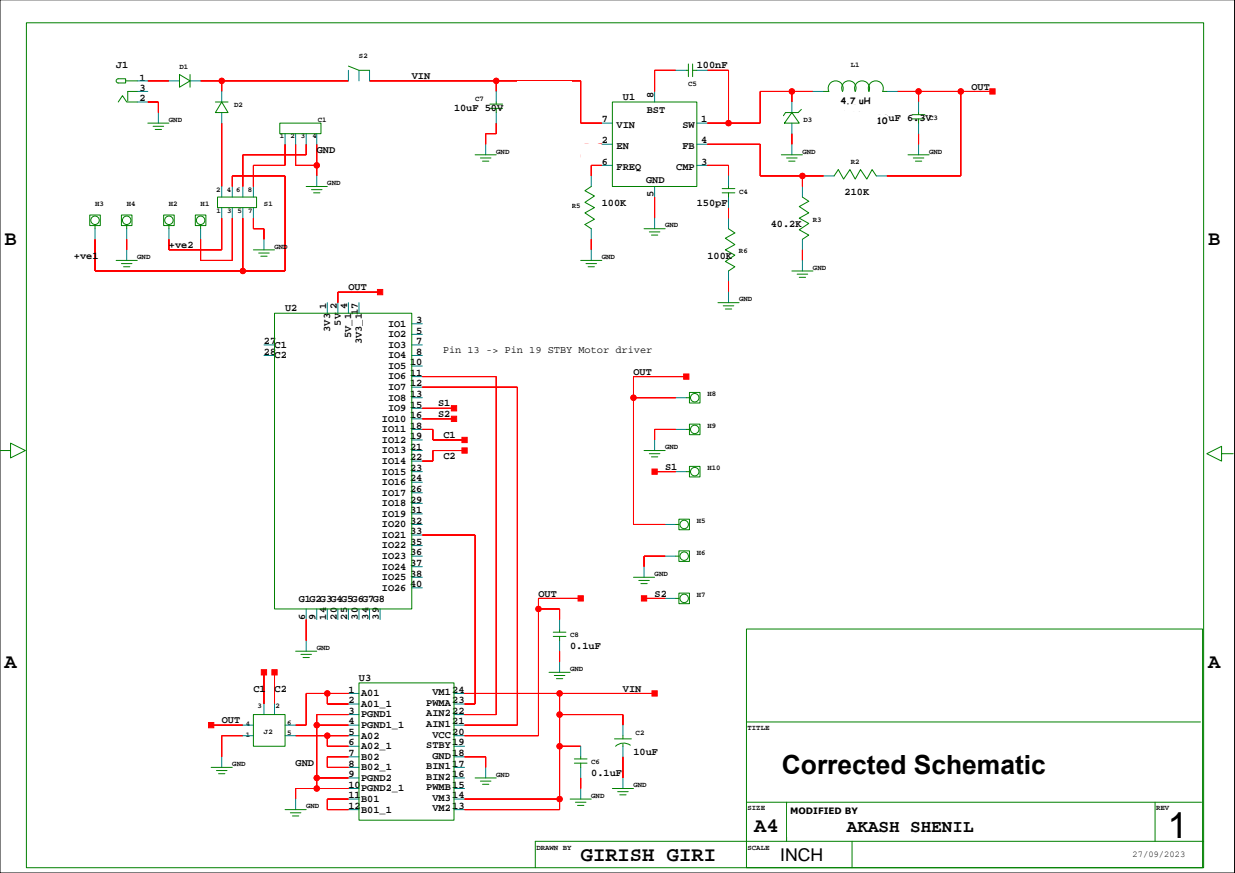
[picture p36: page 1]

Pin 13 -> Pin 19 STBY Motor driver

modified by Akash Shenil
AKASH SHENIL

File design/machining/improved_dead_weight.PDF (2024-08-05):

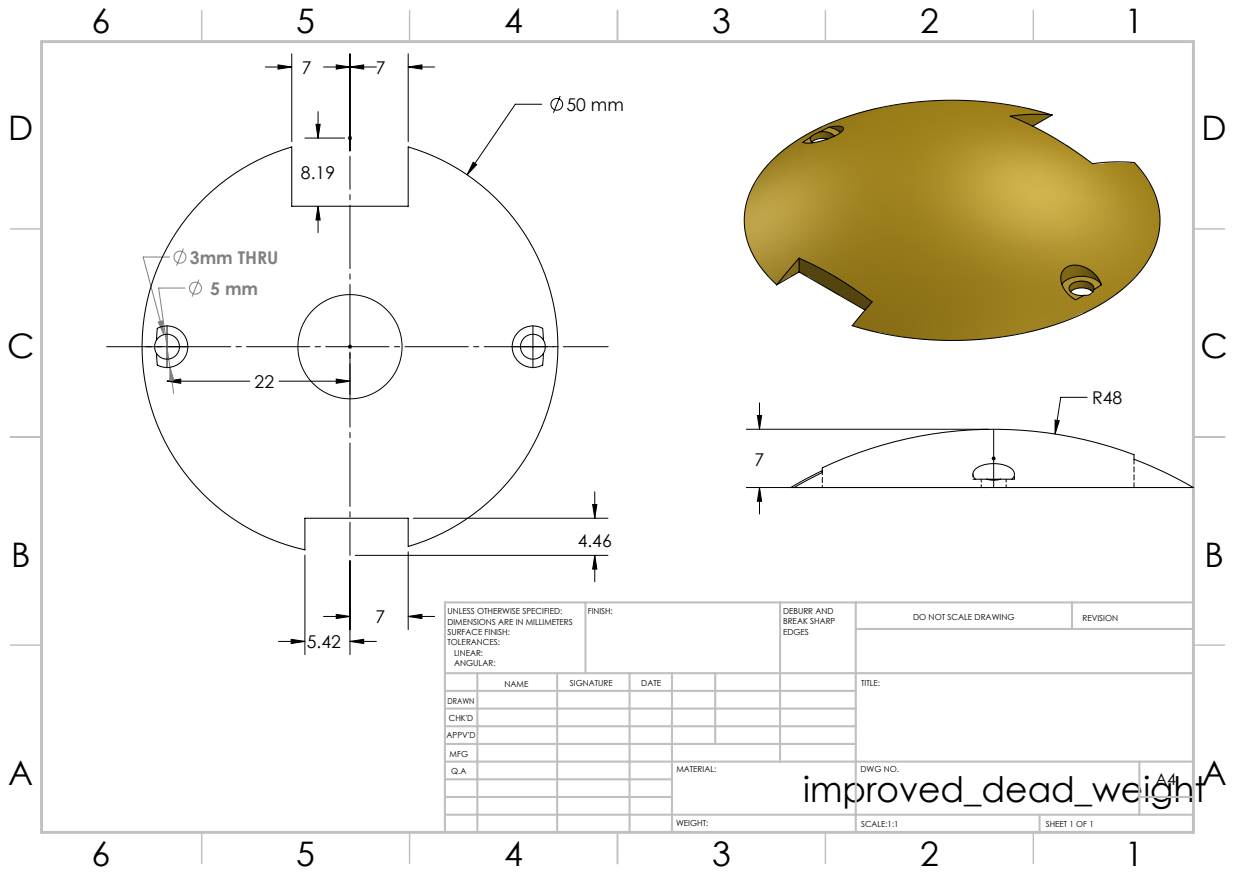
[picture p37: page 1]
3mm THRU; FINISH:; DEBURR AND; BREAK SHARP; DO NOT SCALE DRAWING; REVISION; SCALE:1:1; SHEET 1 OF 1

UNLESS OTHERWISE SPECIFIED:
DIMENSIONS ARE IN MILLIMETERS
SURFACE FINISH:
TOLERANCES:
LINEAR:
ANGULAR:

NAME | SIGNATURE | DATE | | | | TITLE:

DRAWN
CHK'D
APPV'D
MFG
Q.A | | | | MATERIAL: | DWG NO. | A4

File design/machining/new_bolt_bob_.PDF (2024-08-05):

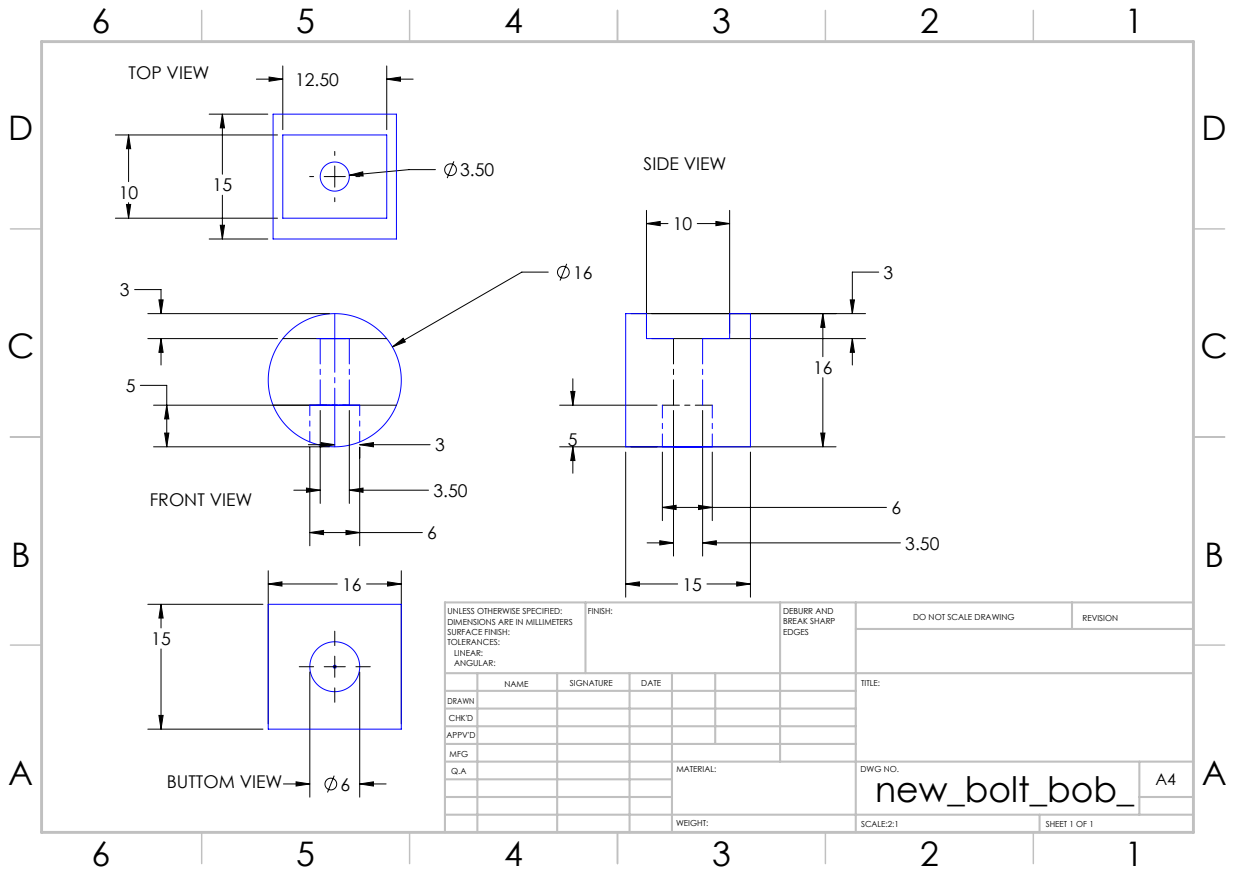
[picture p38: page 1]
FRONT VIEW; BUTTOM VIEW; TOP VIEW; SIDE VIEW; FINISH:; DEBURR AND; BREAK SHARP; DO NOT SCALE DRAWING; REVISION; SCALE:2:1; SHEET 1 OF 1

UNLESS OTHERWISE SPECIFIED:
DIMENSIONS ARE IN MILLIMETERS
SURFACE FINISH:
TOLERANCES:
LINEAR:
ANGULAR:

NAME | SIGNATURE | DATE | TITLE:

DRAWN
CHK'D

MFG
Q.A | MATERIAL: | DWG NO. new_bolt_bob_ | A4

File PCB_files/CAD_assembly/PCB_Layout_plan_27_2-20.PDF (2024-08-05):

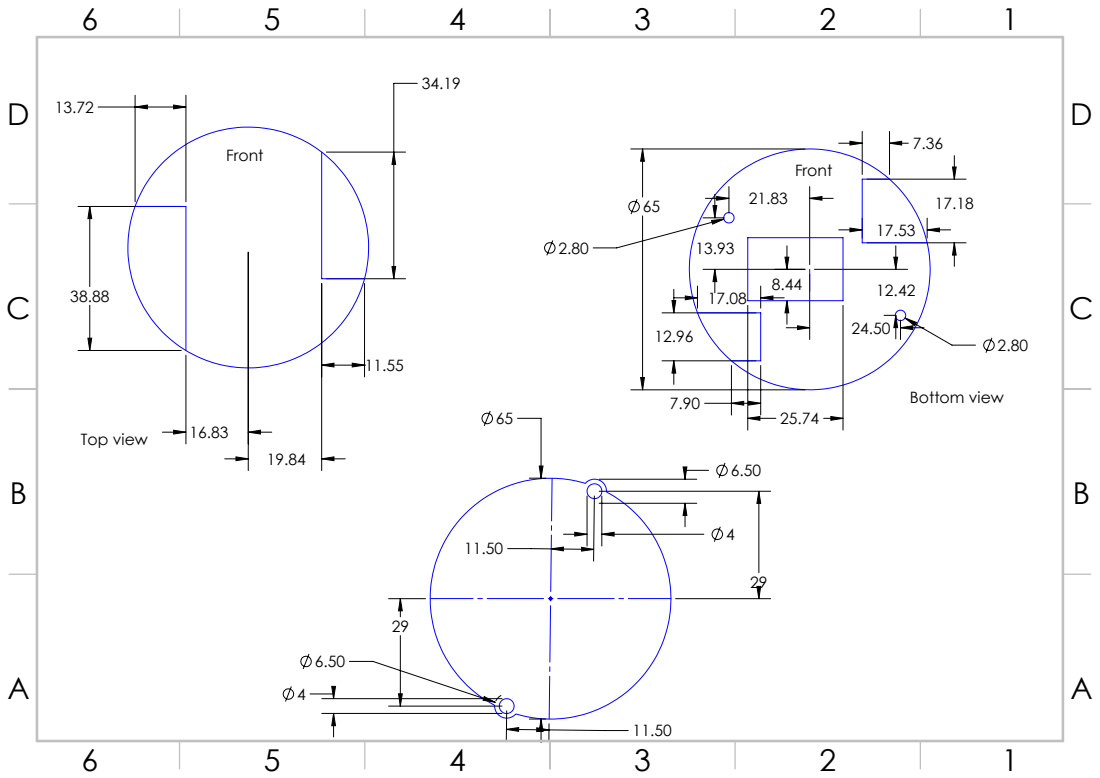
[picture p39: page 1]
Top view; Bottom view

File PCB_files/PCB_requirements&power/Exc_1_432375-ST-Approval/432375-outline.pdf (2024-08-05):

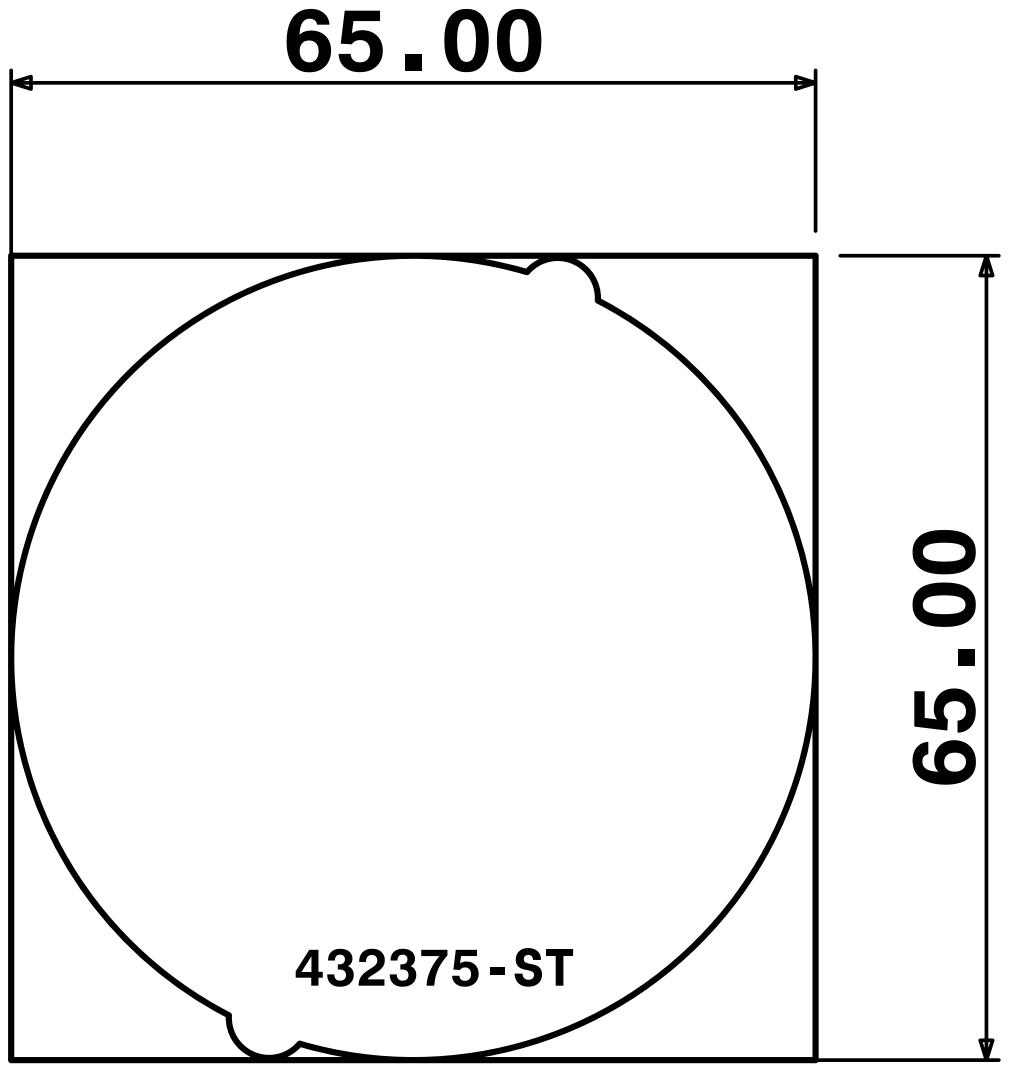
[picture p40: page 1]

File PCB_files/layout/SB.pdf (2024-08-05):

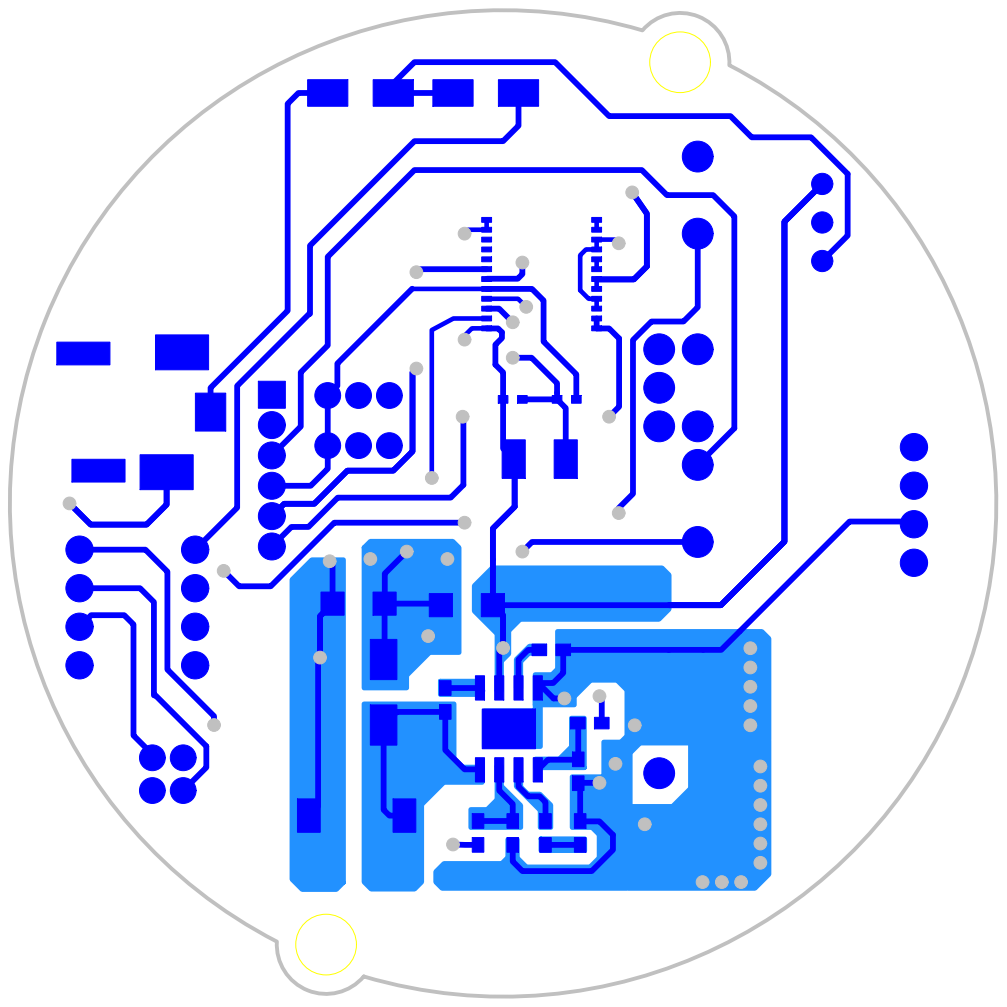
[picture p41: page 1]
C6C⁶x1; C⁶x2; C8C⁸x2; C⁸x1; C4C⁴x1 C⁴x2; C5C⁵x1 C⁵x2; C3C³x1; C³x2; C7C⁷x2; C⁷x1 C2C²x1; C²x2; P1P¹x1 P¹x2 P¹x3 P¹x4; D1D¹x2; D¹x1; D2D²x1; D²x2; D3D³x1 D³x2; S1S¹x1; S¹x2 S¹x3; S¹x4 S¹x5; S¹x6 S¹x7; S¹x8; H1H¹x1; H3H³x1 H2H²x1 H4H⁴x1; H5H⁵x1 H6H⁶x1 H7H⁷x1; H8H⁸x1 H9H⁹x1 H10H¹⁰x1; U1U¹x1; U¹x2; U¹x3; U¹x4 U¹x8; U¹x7; U¹x6; U¹x5 U¹x9; U2U²x2 U²x6 U²x11 U²x12 U²x13 U²x15 U²x16 U²x18 U²x22 U²x33; R1R¹x1 R¹x2; R2R²x1; R²x2; R3R³x1 R³x2; R4R⁴x1 R⁴x2; R5R⁵x2; R⁵x1 R6R⁶x1 R⁶x2; S2S²x1 S²x2 S²x3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

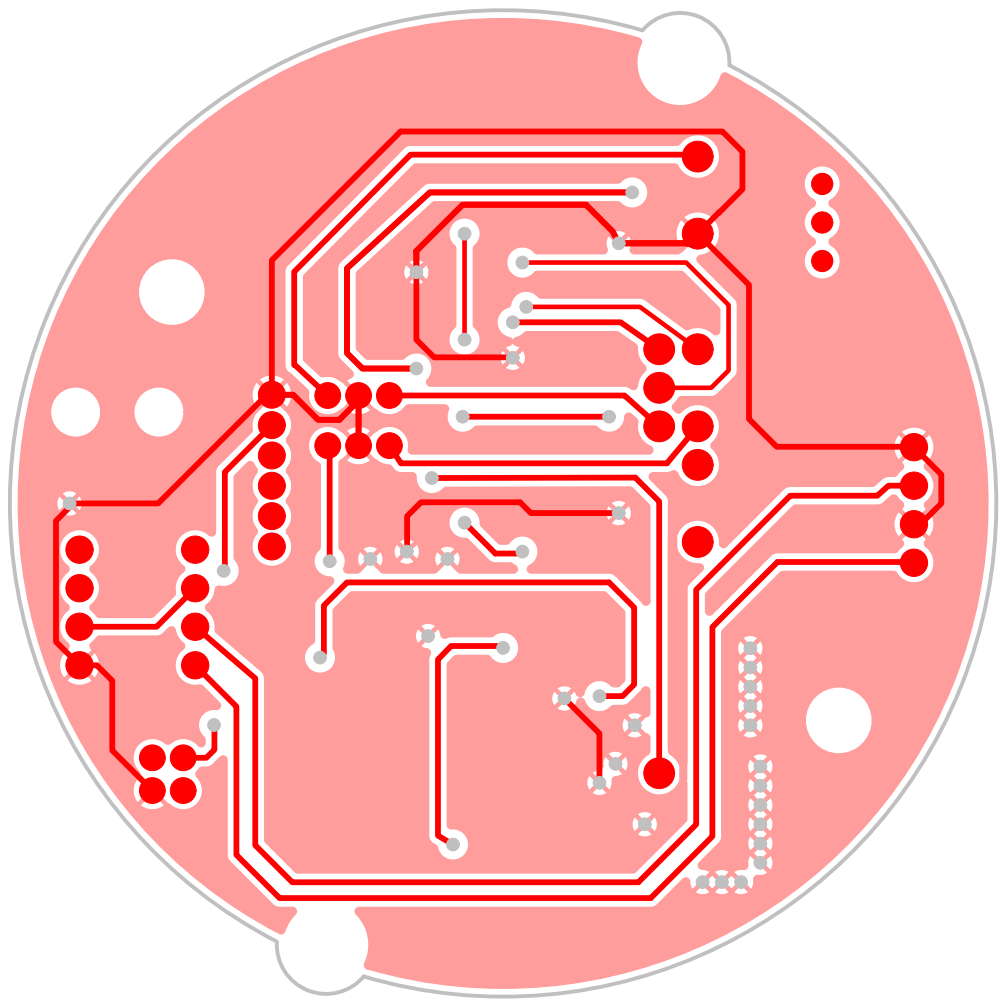
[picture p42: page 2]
P1P¹x1 P¹x2 P¹x3 P¹x4; S1S¹x1; S¹x2 S¹x3; S¹x4 S¹x5; S¹x6 S¹x7; S¹x8; H1H¹x1; H3H³x1 H2H²x1 H4H⁴x1; H5H⁵x1 H6H⁶x1 H7H⁷x1; H8H⁸x1 H9H⁹x1 H10H¹⁰x1; U2U²x2 U²x6 U²x11 U²x12 U²x13 U²x15 U²x16 U²x18 U²x22 U²x33; S2S²x1 S²x2 S²x3

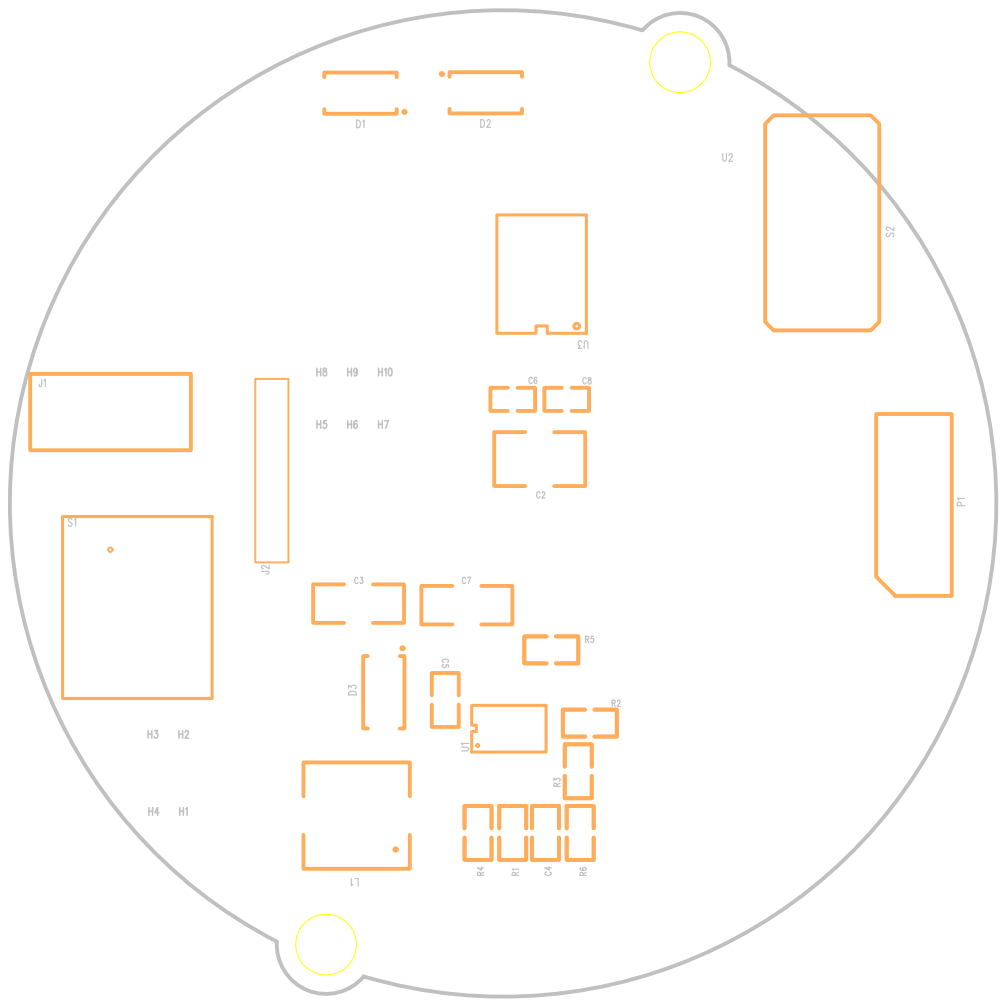
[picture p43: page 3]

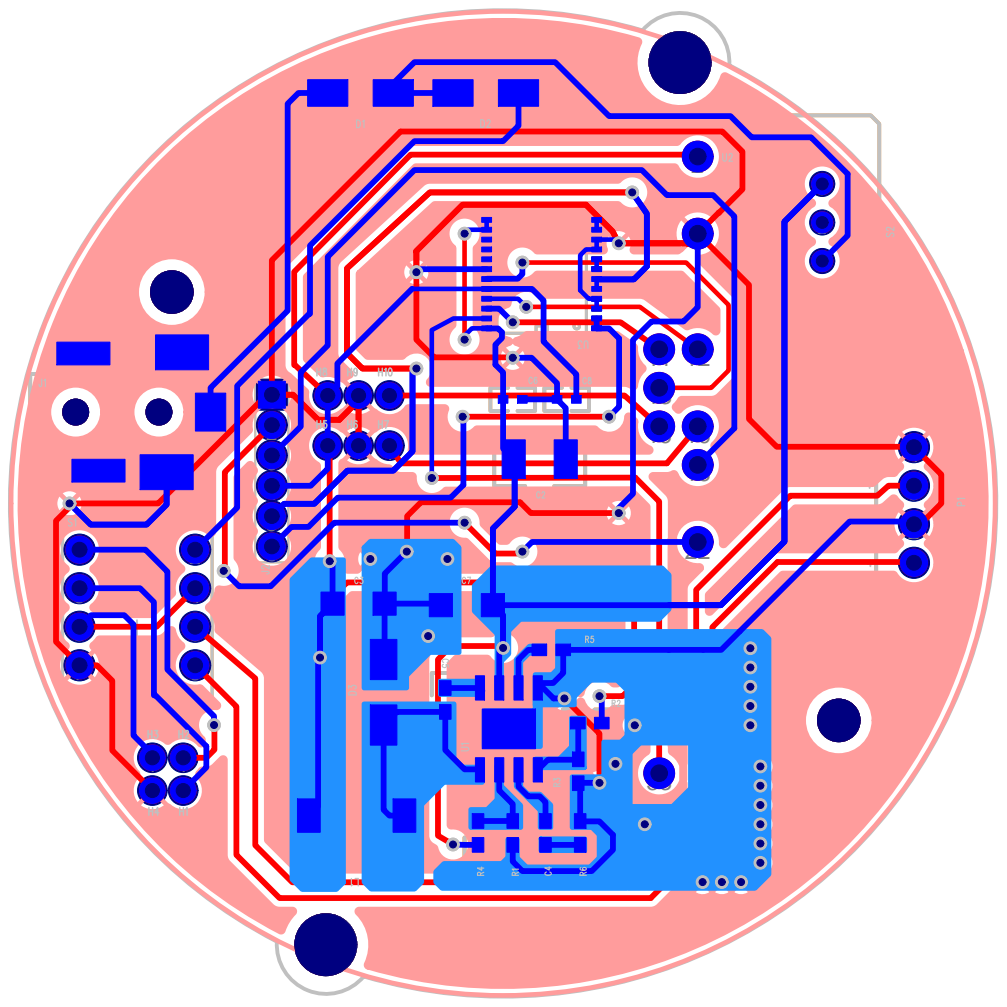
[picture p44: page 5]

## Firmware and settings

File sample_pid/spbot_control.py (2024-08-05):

# Servo Control
import time
import pigpio
import socket
import sys
import board
import busio
import adafruit_bno055
import datetime
import csv

from scipy.signal import find_peaks
#import matplotlib.pyplot as plt
#import matplotlib.animation as animation

# Use these lines for I2C IMU feedback
i2c = busio.I2C(board.SCL, board.SDA)
sensor = adafruit_bno055.BNO055_I2C(i2c)


#Setting up pwm for servo
pi =  pigpio.pi()                    
pi.set_mode(22, pigpio.OUTPUT)
pi.set_mode(23, pigpio.OUTPUT)

pitch_data=[]
roll_data=[]
yaw_data=[]
timestamp_data=[]
#  Setting up the N20 motor  
#pi.setmode(GPIO_ pin number, IN/OUT)

pi.set_mode(13,pigpio.OUTPUT)  #PWMA 13        7
pi.set_mode(17,pigpio.OUTPUT)  #AIN2 17       11
pi.set_mode(18,pigpio.OUTPUT)  #AIN1 18        12
pi.set_mode(27,pigpio.OUTPUT)  #STBY 27        13

global roll_actual

class PIDController:
    def __init__(self, kp, kd, ki, setpoint):
        self.kp = kp
        self.ki = ki
        self.kd = kd
        self.setpt = setpoint
        self.prev_err = 0
        self.integral = 0
    
    def update(self, error, dt):
        derivative = (error-self.prev_err) / dt
        self.integral += error * dt
        pid_output = self.kp * error + self.ki * self.integral + self.kd * derivative
        self.prev_err = error
        return pid_output
    

Kp = 2.0
Kd = 0.3
Ki = 1.3

setpnt = 0.0

pidcontrol = PIDController(kp=Kp, ki=Ki, kd=Kd, setpoint=setpnt)
    
    
def map(value, axes_min, axes_max, actuate_min, actuate_max):
    axes_span = axes_max-axes_min
    actuate_span = actuate_max-actuate_min
    value_scaled = (float(value - axes_min)/float(axes_span))
    return int(actuate_min+(value_scaled*actuate_span))


def front_servo(angle):

    #angle here is negated because its in opposite direction facing
    pulse_width = map(-angle, -30, 30, 1300, 2000) 
    pi.set_servo_pulsewidth(22, pulse_width)

def rear_servo(angle):

    pulse_width = map(angle, -30, 30, 1000, 1800)
    pi.set_servo_pulsewidth(23, pulse_width)

def get_pitch():
	yaw, roll, pitch = sensor.euler
	print('Im geting pitch ',pitch)
	return pitch

def get_yaw():
	yaw, roll, pitch = sensor.euler
	print('Im geting yaw ',yaw)
	return yaw

def get_roll():
	yaw, roll, pitch = sensor.euler
	print('Im geting roll ',roll)
	return roll

# def roll_control():
# 	Kp = 1
# 	P = Kp*roll_err
# 	front_servo(P)
# 	rear_servo(P)
# 	print('Im in roll controller P ',P) 

def forward_ascent():
	for pwm_a in range(80,0, -10):
		motor(True, pwm_a)
		time.sleep(0.25)

def backward_descent():
	for pwm_b in range(80,0, -10):
		motor(False, pwm_b)
		time.sleep(0.25)

def motor(mot_dir, mot_pwm):

    if(mot_dir == True ) :
        pi.write(27,1)        #disable standby active low
        pi.write(18,0)
        pi.write(17,1)
        pi.set_PWM_dutycycle(13,mot_pwm)


    elif(mot_dir == False) :
        pi.write(27,1)        #disable standby active low
        pi.write(18,1)
        pi.write(17,0)
        pi.set_PWM_dutycycle(13,mot_pwm)

    else:
        pi.write(18,0)
        pi.write(17,0)
        pi.set_PWM_dutycycle(13, 0)
        pi.write(27,0)

#fig, ax = plt.subplots()
#line, = ax.plot([], [], 'r-', label='Roll')
#setpoint_line, = ax.plot([], [], 'b--', label='Setpoint')
#ax.set_ylim(-40, 40)
#ax.set_xlim(0, 100)
#ax.set_xlabel('Time')
#ax.set_ylabel('Roll')
#ax.legend()
#ax.grid()

#def init():
 #   line.set_data([], [])
 #   setpoint_line.set_data([], [])
 #   return line, setpoint_line

#def update_plot():
#    roll_actual = get_roll()
#    error = setpnt - roll_actual
#    dt = 0.1  # Adjust time step as needed
#    ctrl_signal = pidcontrol.update(error=error, dt=dt)
#    front_servo(ctrl_signal)
#    rear_servo(ctrl_signal)

#    roll_data.append(roll_actual)
#    timestamp_data.append(len(roll_data) * dt)  # Using the length of roll_data to approximate time
#    line.set_data(timestamp_data, roll_data)
#    setpoint_line.set_data(timestamp_data, [setpnt]*len(timestamp_data))

#    return line, setpoint_line

#ani = animation.FuncAnimation(fig, update_plot, init_func=init, blit=True, interval=100)

#plt.show()

def write_to_csv(data, filename):
    with open(filename, mode='a', newline='') as file:
        writer = csv.writer(file)
        writer.writerow(data)

with open('output.csv', mode='w', newline='') as file:
    writer = csv.writer(file)
    writer.writerow(['roll', 'pitch', 'yaw', 'time'])  # Write header
    for row in pitch_data:
        writer.writerow(row)

def calculate_oscillation_period(roll_data, timestamp_data):
    peaks, _ = find_peaks(roll_data)
    if len(peaks) > 1:
        periods = [(timestamp_data[peaks[i]] - timestamp_data[peaks[i-1]]).total_seconds() for i in range(1, len(peaks))]
        Pu = sum(periods) / len(periods) if periods else 0
        return Pu
    return None

#Setting up Servo for Android control
'''HOST = ''
PORT = 6000
s = socket.socket(socket.AF_INET, socket.SOCK_STREAM)
print ("socket created.")
try:
        s.bind((HOST,PORT))
except socket.error as msg:
        print ('Bind failed. Error code: ' + str(msg))
        sys.exit()
print ('Socket bind complete')
s.listen(10)
print ('socket now listening')
conn, addr = s.accept()

flag_run = False

'''
try:
    while True:
        x=0
        y=6.5
        dt = 0.25
        
        mot_pwm = map(y,-65,65, 20, 110)
        mot_dir = True
        print("Forward")
        motor(mot_dir, mot_pwm)
        flag_run = True
        
        roll_actual = get_roll()
        error = setpnt - roll_actual    
        ctrl_signal = pidcontrol.update(error=error, dt=dt)
        front_servo(ctrl_signal)
        rear_servo(ctrl_signal)
        
        pitch_actual= get_pitch()
        yaw_actual= get_yaw()
        roll_data.append(roll_actual)
        timestamp = datetime.datetime.now() 
        timestamp_data.append(timestamp)
        pitch_data.append([roll_actual,pitch_actual,yaw_actual, timestamp])

        if len(roll_data) > 20:  # Analyze data after collecting enough points
            Pu = calculate_oscillation_period(roll_data, timestamp_data)
            if Pu:
                print(f"Current Oscillation Period (Pu): {Pu:.2f} seconds")


       # for row in pitch_data:
           # write_to_csv(row, 'output.csv')
        
        time.sleep(dt)

except KeyboardInterrupt:
    motor(False,0)
    print ('Socket is now closing')
    #conn.close()
    pi.stop()
